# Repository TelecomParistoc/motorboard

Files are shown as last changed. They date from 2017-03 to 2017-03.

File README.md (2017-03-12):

# motorboardv2
carte permettant de piloter les moteurs et de suivre la position actuelle

## Objectifs
La carte devra répondre aux objectifs suivant :

* permettre l'asservissement en position des moteurs, contrôlé par le Raspberry Pi
* controler l'IMU et faire la fusion avec les roues codeuses pour contre-balancer le lag du BNO055
* faire la fusion de la radio, de l'IMU et des roues codeuses pour obtenir la position absolue

## Vue Système

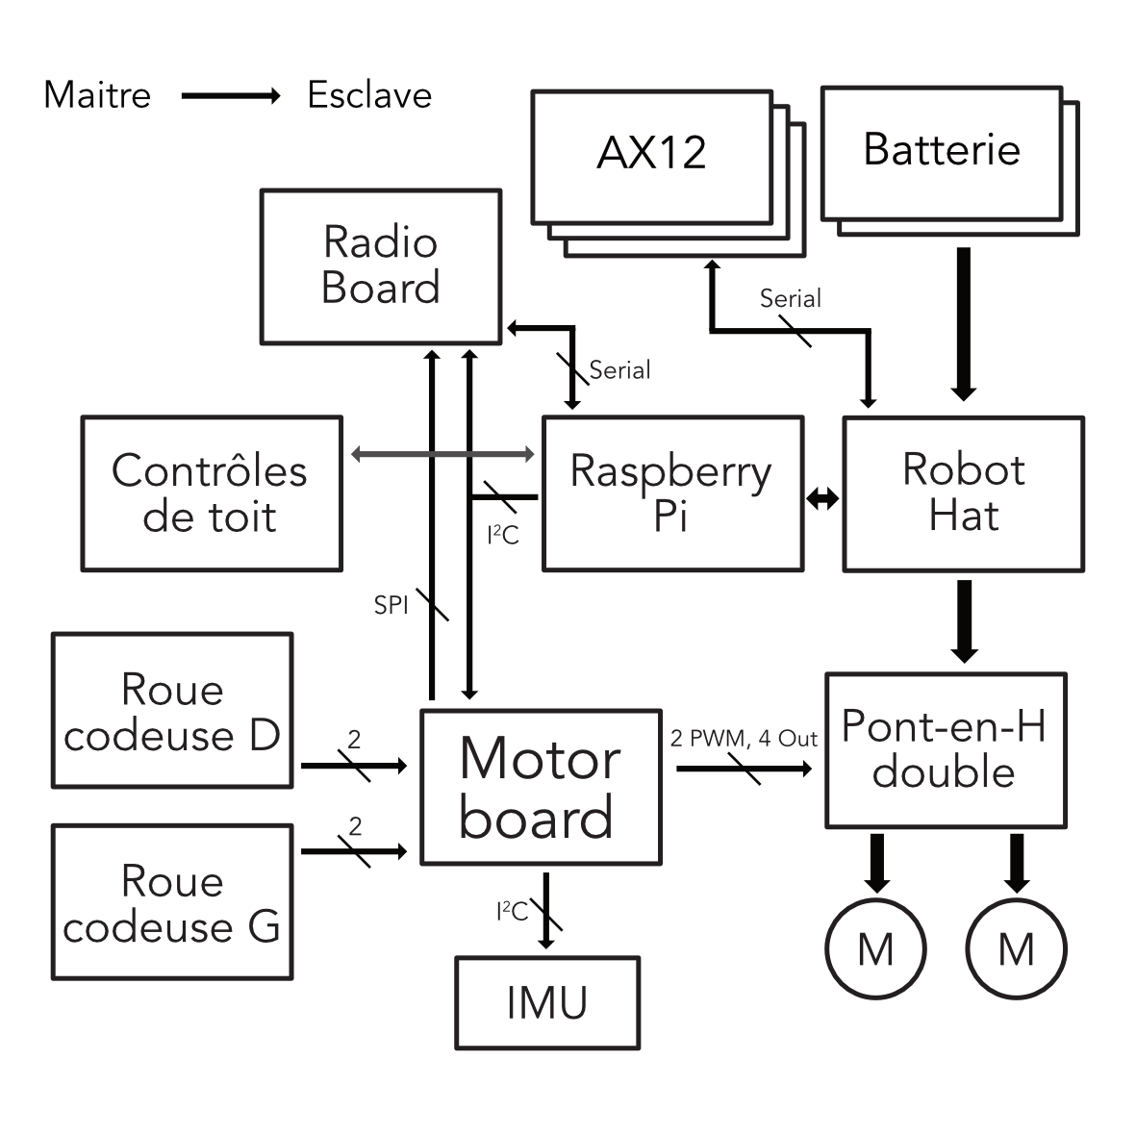
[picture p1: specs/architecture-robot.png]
archi robot


En plus des liens vers les roues codeuses et le pont-en-H, il est nécessaire de fournir 3 ports :
* Un port esclave sur le bus I2C principal du robot, permettant la communication avec le Raspberry Pi
* Un port maitre SPI pour une liaison direct rapide à faible latence avec la carte radio
* un port I2C maitre pour contrôler l'IMU

La carte n'est pas responsable de l'alimentation de puissance du pont-en-H et les moteur mais fourni l'alimentation logique.

## Contraintes

#### MC1 Configuration des connecteurs
Afin d'assurer la compatibilité avec les éléments existants, la configuration des connecteurs est spécifiée dans [motorboard connectors.pdf](https://github.com/TelecomParistoc/motorboardv2/blob/master/specs/motorboard%20connectors.pdf)

#### MC2 Emplacement des trous de fixation
La carte sera montée au dessus de la carte pont-en-H existante, les trous de fixation devront donc être alignés pour permettre le passage des vis.

## Solution proposée

### Contrôleur

Afin de rendre le portage du code existant facile et d'accélerer le développement, la série STM32F302x8/6 a été sélectionnée. 
Le **STM32F302C8** a été retenu.

| MCU | STM32F302C8T6 |
| ----- | --- |
| Coeur | Cortex M4F |
| Horloge | Interne 64MHz |
| Flash | 64Ko |
| RAM | 16Ko |
| SPI | 2 |
| I2C | 3 |
| boitier | LQFP48 |

### Alimentation

| Sous-système | Consommation max. |
| --- | --- |
| LED (5V) | 1 mA |
| Roues codeuses (5V) | 120 mA |
| **Total 5V** | **121 mA** |
| Logique pont-en-H (3.3V) | 8 mA |
| IMU (3.3V) | 12.5 mA |
| Contrôleur (3.3V) | 42 mA |
| LEDs (3.3V) | 3.5 mA |
| **Total 3.3V** | **66 mA** |

La consommation maximum sur le 3.3V est jugée raisonnable, il n'est pas nécessaire d'ajouter un régulateur local.

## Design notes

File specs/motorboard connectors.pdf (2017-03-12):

Motor Board | Connectors

## Connector pin mapping :

## H-bridge board connector (MOTOR) :

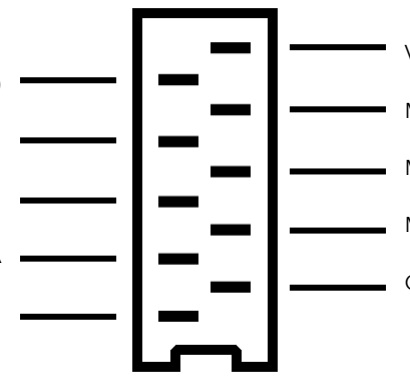
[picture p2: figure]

## Main I2C bus connectors (RPI and RPI2) :

VCC (3.3V)

MOTOR1 INA

MOTOR1 PWM

MOTOR1 INB

GND

VCC (3.3V)

LMOTOR INB

L MOTOR PWM

L MOTOR INA

GND

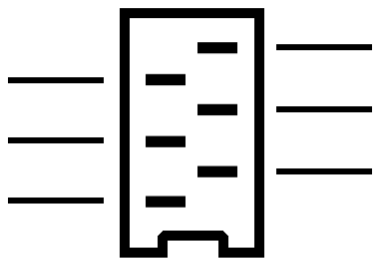
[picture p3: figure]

+5V

GND

SCL

+3.3V

SDA

n_RESET

## SPI link to radio board (RADIO) :

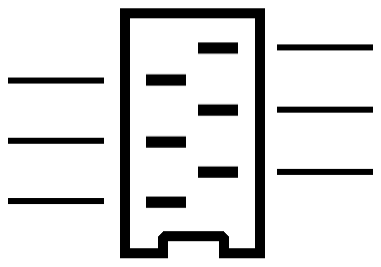
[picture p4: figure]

## Encoder wheels link (RCOD and LCOD) :

B CHANNEL

+5V

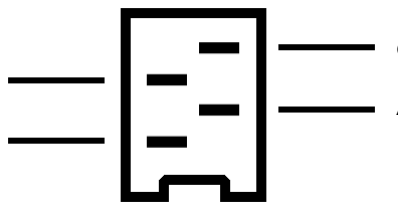
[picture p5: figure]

GND

A CHANNEL

MOSI

SCK

GND

MISO

nCS

GND

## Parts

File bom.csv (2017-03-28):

Qty | Qty to buy | Value | Device | Package | Parts | Description | Distributor
3 | 0 |  | LEDCHIPLED_0805 | CHIPLED_0805 | 3V3 5V RUN | LED
1 | 0 |  | MA06-1 | MA06-1 | IMU | PIN HEADER
1 | 0 |  | SMDTOP-10 | SMDTOP10 | MOTOR | AMP connector
2 | 0 |  | SMDTOP-4 | SMDTOP4 | LCOD RCOD | AMP connector
4 | 0 | 100nF | C-EUC0805 | C0805 | C1 C2 C3 C6 | CAPACITOR
1 | 0 | 1k | R-US_M0805 | M0805 | R11 | RESISTOR
1 | 0 | 2.2k | R-US_M0805 | M0805 | R10 | RESISTOR
1 | 0 | 4.7k | R-US_M0805 | M0805 | R9 | RESISTOR
1 | 1 | 4.7uF | C-EUC0805 | C0805 | C5 | CAPACITOR | FARNELL 1759420
1 | 1 | 10uF | C-EUC0805 | C0805 | C4 | CAPACITOR | FARNELL 2320856
1 | 1 | STM32F302_303C2 | STM32F302_303C2 | LQFP48-7X7MM | U1 |  | MOUSER 511-STM32F302C8T6
1 | 1 | SWD/JTAG-_PINS | SWD/JTAG-_PINS | SAMTEC_SHF-105-01-L-D-SM | U$1 |  | FARNELL 1885915
3 | 3 |  | SMDTOP-6 | SMDTOP6 | RADIO RPI RPI2 | AMP connector | FARNELL 2473376 FARNELL 2473358

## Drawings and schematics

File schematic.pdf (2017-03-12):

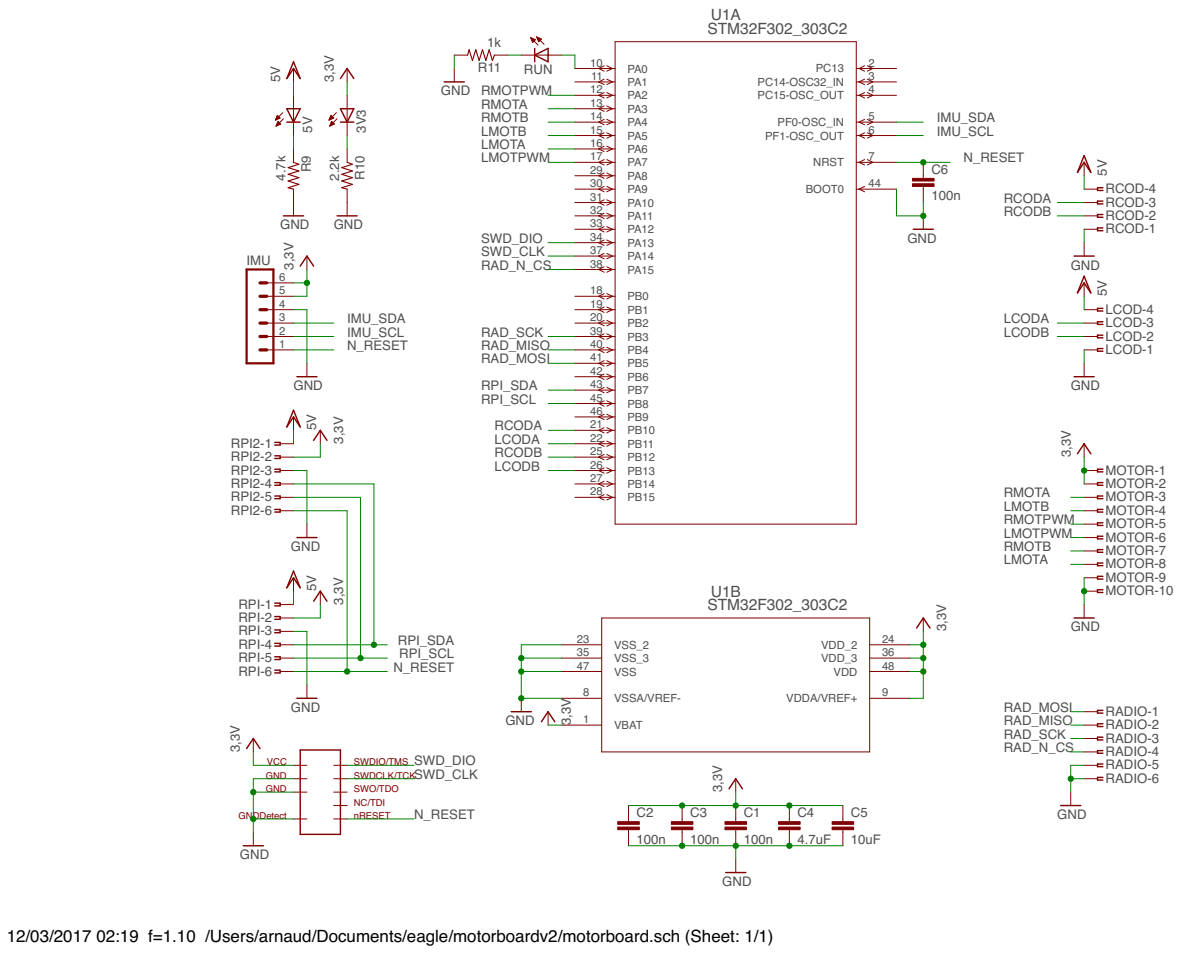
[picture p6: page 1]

35 | | 36
47 | | 48

VSSA/VREF- 8 | 9

VCC GND GND GNDDetect

12/03/2017 02:19 f=1.10 /Users/arnaud/Documents/eagle/motorboardv2/motorboard.sch (Sheet: 1/1)

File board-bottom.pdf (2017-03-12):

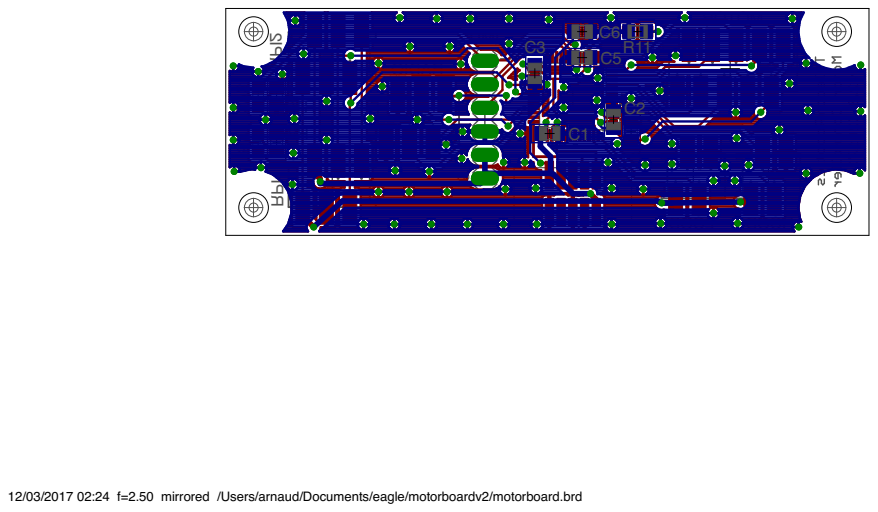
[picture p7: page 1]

12/03/2017 02:24 f=2.50 mirrored /Users/arnaud/Documents/eagle/motorboardv2/motorboard.brd

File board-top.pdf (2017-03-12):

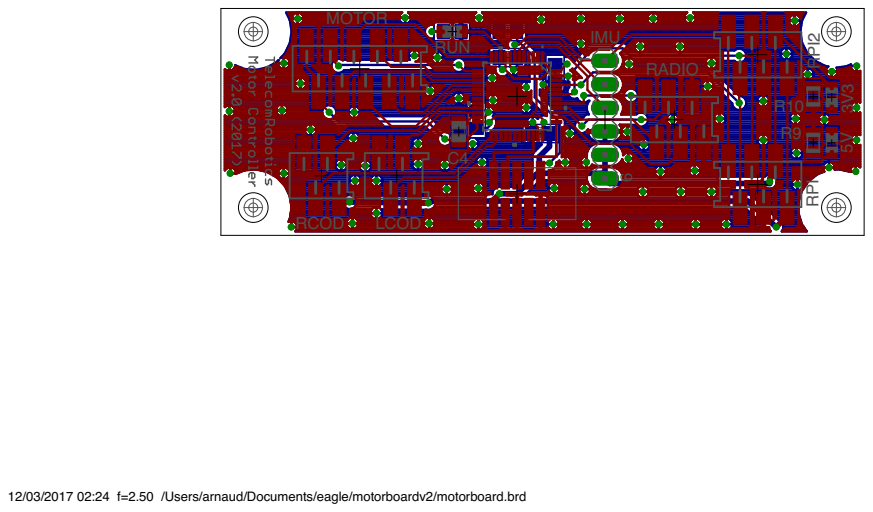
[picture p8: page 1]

12/03/2017 02:24 f=2.50 /Users/arnaud/Documents/eagle/motorboardv2/motorboard.brd

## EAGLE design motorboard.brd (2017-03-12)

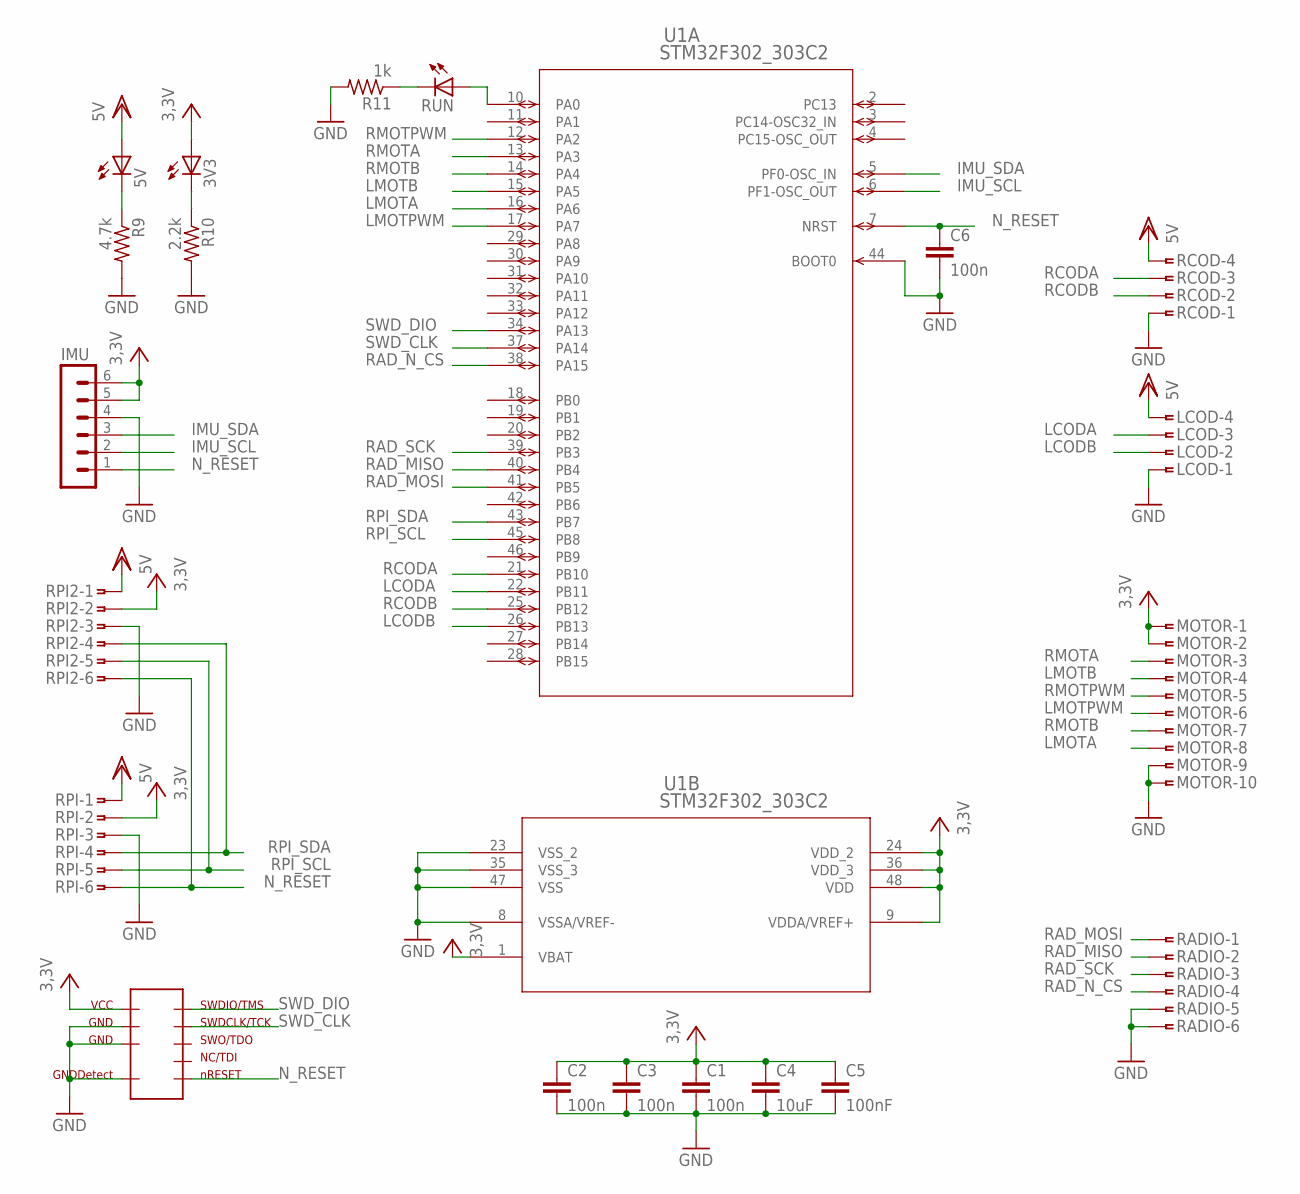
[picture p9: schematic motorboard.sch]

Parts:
3V3, 5V: LEDCHIPLED_0805; CHIPLED_0805
C1, C2, C3, C6: 100n; C0805
C4: 10uF; C0805
C5: 100nF; C0805
IMU: MA06-1
LCOD: SMDTOP-4; SMDTOP4
MOTOR: SMDTOP-10; SMDTOP10
R9: 4.7k; M0805
R10: 2.2k; M0805
R11: 1k; M0805
RADIO: SMDTOP-6; SMDTOP6
RCOD: SMDTOP-4; SMDTOP4
RPI, RPI2: SMDTOP-6; SMDTOP6
RUN: LEDCHIPLED_0805; CHIPLED_0805
U1: STM32F302_303C2; LQFP48-7X7MM
U$1: SWD/JTAG-_PINS; SAMTEC_SHF-105-01-L-D-SM

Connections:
GND: C1.2, C2.2, C3.2, C4.2, C5.2, C6.2, IMU.4, LCOD.1, MOTOR.9, MOTOR.10, R9.2, R10.2, R11.2, RADIO.5, RADIO.6, RCOD.1, RPI.3, RPI2.3, U1.8 (VSSA/VREF-), U1.23 (VSS_2), U1.35 (VSS_3), U1.44 (BOOT0), U1.47 (VSS), U$1.P$3, U$1.P$5, U$1.P$9
IMU_SCL: IMU.2, U1.6 (PF1-OSC_OUT)
IMU_SDA: IMU.3, U1.5 (PF0-OSC_IN)
LCODA: LCOD.3, U1.22 (PB11)
LCODB: LCOD.2, U1.26 (PB13)
LMOTA: MOTOR.8, U1.16 (PA6)
LMOTB: MOTOR.4, U1.15 (PA5)
LMOTPWM: MOTOR.6, U1.17 (PA7)
unnamed: RUN.A, U1.10 (PA0)
unnamed: R11.1, RUN.C
unnamed: 5V.C, R9.1
unnamed: 3V3.C, R10.1
N_RESET: C6.1, IMU.1, RPI.6, RPI2.6, U1.7 (NRST), U$1.P$10
RAD_MISO: RADIO.2, U1.40 (PB4)
RAD_MOSI: RADIO.1, U1.41 (PB5)
RAD_N_CS: RADIO.4, U1.38 (PA15)
RAD_SCK: RADIO.3, U1.39 (PB3)
RCODA: RCOD.3, U1.21 (PB10)
RCODB: RCOD.2, U1.25 (PB12)
RMOTA: MOTOR.3, U1.13 (PA3)
RMOTB: MOTOR.7, U1.14 (PA4)
RMOTPWM: MOTOR.5, U1.12 (PA2)
RPI_SCL: RPI.5, RPI2.5, U1.45 (PB8)
RPI_SDA: RPI.4, RPI2.4, U1.43 (PB7)
SWD_CLK: U1.37 (PA14), U$1.P$4
SWD_DIO: U1.34 (PA13), U$1.P$2
VCC: 3V3.A, C1.1, C2.1, C3.1, C4.1, C5.1, IMU.5, IMU.6, MOTOR.1, MOTOR.2, RPI.2, RPI2.2, U1.1 (VBAT), U1.9 (VDDA/VREF+), U1.24 (VDD_2), U1.36 (VDD_3), U1.48 (VDD), U$1.P$1
VDD: 5V.A, LCOD.4, RCOD.4, RPI.1, RPI2.1

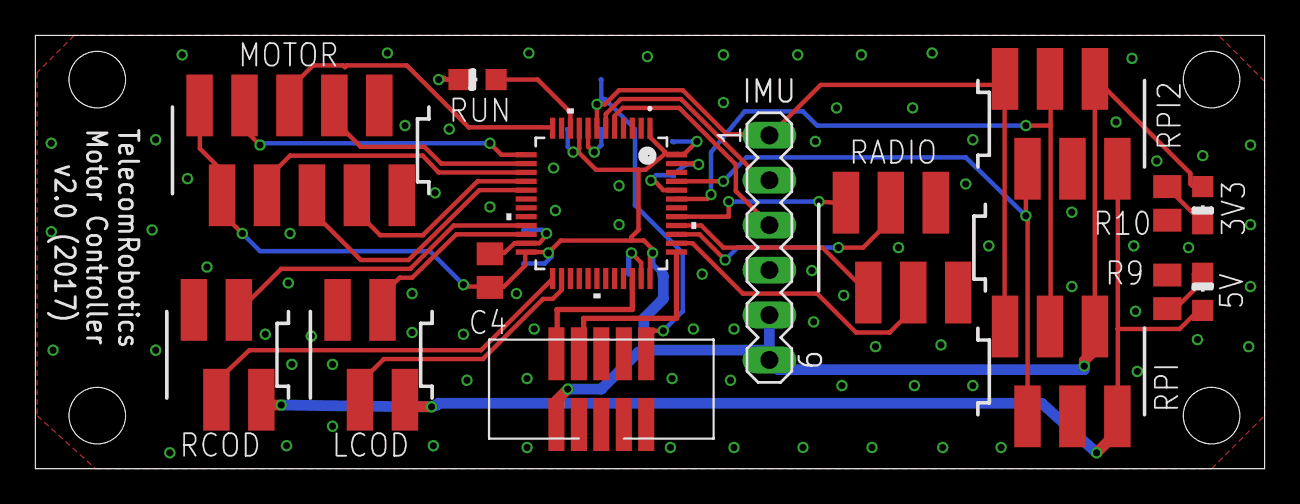
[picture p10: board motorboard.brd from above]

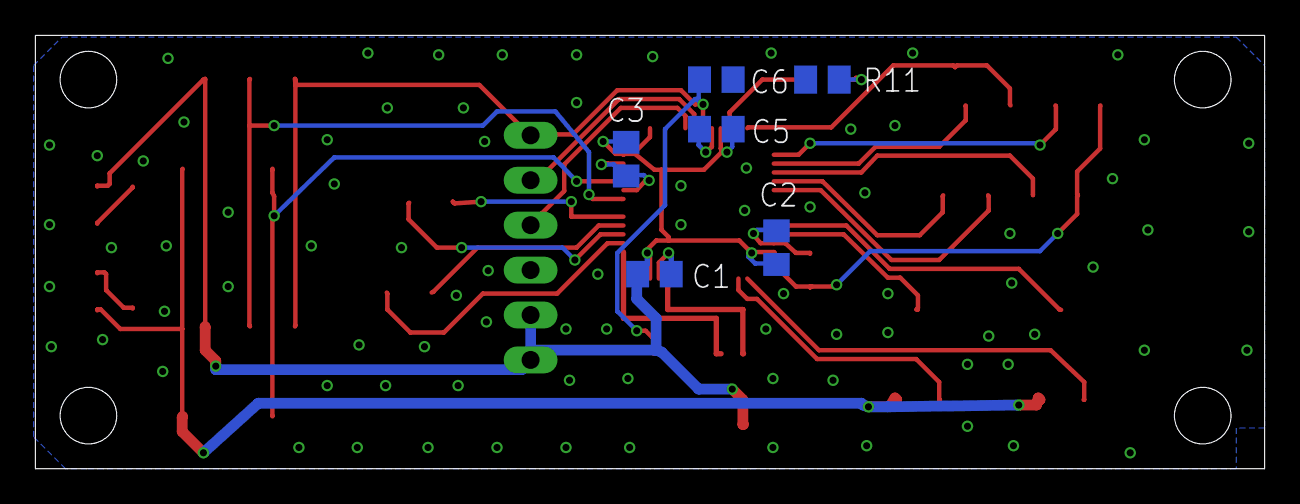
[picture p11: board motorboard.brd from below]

Board: 2 copper layers, 69.5 x 24.5 mm, 21 parts (6 on the bottom side), 28 nets.

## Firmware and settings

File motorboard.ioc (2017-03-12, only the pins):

Mcu.UserName=STM32F302C8Tx
PA0.Signal=GPIO_Output
PA13.Signal=SYS_JTMS-SWDIO
PA14.Signal=SYS_JTCK-SWCLK
PA15.Signal=GPIO_Output
PA2.Signal=S_TIM15_CH1
PA3.Signal=S_TIM15_CH2
PA4.Signal=GPIO_Output
PA5.Signal=GPIO_Output
PA6.Signal=S_TIM16_CH1
PA7.Signal=S_TIM17_CH1
PB10.Signal=S_TIM2_CH3
PB11.Signal=S_TIM2_CH4
PB12.Signal=GPIO_Input
PB13.Signal=GPIO_Input
PB3.Signal=SPI3_SCK
PB4.Signal=SPI3_MISO
PB5.Signal=SPI3_MOSI
PB7.Signal=I2C1_SDA
PB8.Signal=I2C1_SCL
PF0-OSC_IN.Signal=I2C2_SDA
PF1-OSC_OUT.Signal=I2C2_SCL

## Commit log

2017-03-12 schematics and board v1, added connectors spec
    [motorboard.brd, motorboard.sch]
2017-03-12 added pdf of board and schematics
2017-03-12 hidden retrict areas
    [motorboard.brd]
2017-03-12 fixed problems shown by Eurocircuit pcbview
    [motorboard.brd]
2017-03-12 fixed capacitors values
    [motorboard.brd, motorboard.sch]
2017-03-12 added BOM
    [bom.xls, motorboard.sch]
2017-03-19 added distributor refs to bom
    [bom.csv, bom.xls]

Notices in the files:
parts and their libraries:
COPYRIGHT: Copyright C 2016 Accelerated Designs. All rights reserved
